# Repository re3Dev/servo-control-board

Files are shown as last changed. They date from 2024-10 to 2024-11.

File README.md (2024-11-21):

# servo-control-board
Breakout PCB for connecting external stepper/servo motor drivers.

- Takes digital pins from the Archimajor board (3.3V) and shifts voltage (0-50V) according to input using power drivers. 
- Maximum of 11 motors: 7 external, 4 TMC5160
- Display reads out supplied voltage for redundency.
- Pinout is simple and single-ended. Assuming motor driver takes step/pulse, direction, and enable. Currently no support for HLFB.
- Extra +5V and +3.3V output pins
- The main purpose of the project is to drive external servo motors, but other digital I/O devices can be used.

Soldered-V0 3

- Digital pins are taken from Serial 5V+, SC1, SC2, and step/dir header of the Archimajor board:
  




- NOTE:
  - The step/dir header on the archimajor are used for the last four stepper drivers.
  - These pins can be reassigned for external motors on the breakout board.
  - You cannot simultaneously drive an external motor and use the embedded drivers.

Archimajor_motors

- Design is made to primarily support Teknic Clearpath SD series motors.

clearpath_inputs

- Using single-ended connections (will need to invert logic):
  - A+ = Digital
  - B+ = Digital
  - EN+ = Digital
  - A- = GND
  - B- = GND
  - EN- = GND

- Pinout:
  - Motor1:
    - A+ = PA1
    - B+ = PC2
    - EN+ = PA28
  - Motor2:
    - A+ = PB13
    - B+ = PA0
    - EN+ = PB2
  - Motor3:
    - A+ = PB12
    - B+ = PA5
    - EN+ = PB25
  - Motor4:
    - A+ = PB27
    - B+ = PA3
    - EN+ = PB6
  - Motor5:
    - A+ = PB8
    - B+ = PB22
    - EN+ = PB3
  - Motor6:
    - A+ = PD3
    - B+ = PB24
    - EN+ = PB26
  - Motor7:
    - A+ = PA8
    - B+ = PA9
    - EN+ = PC8

top_unsoldered-V0 3
bottom_unsoldered-V0 3

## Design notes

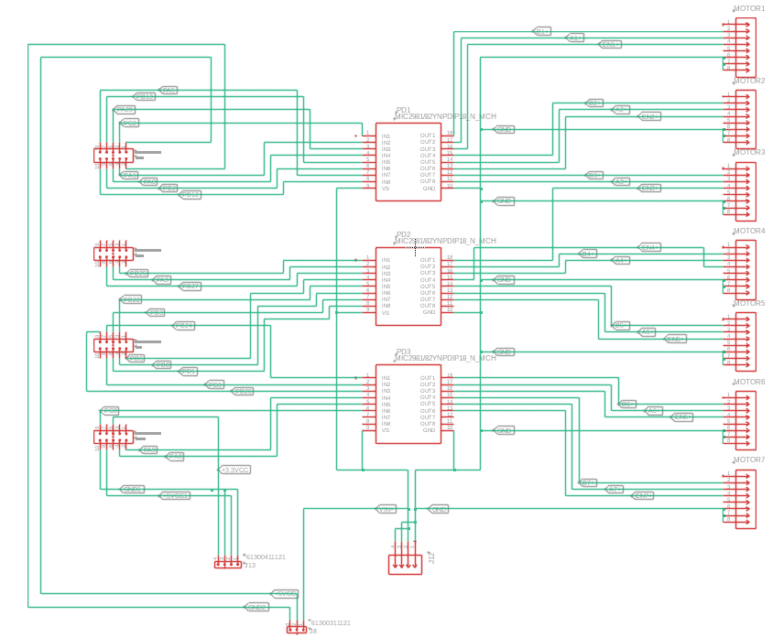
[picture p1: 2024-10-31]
Schematic_V0.3.png

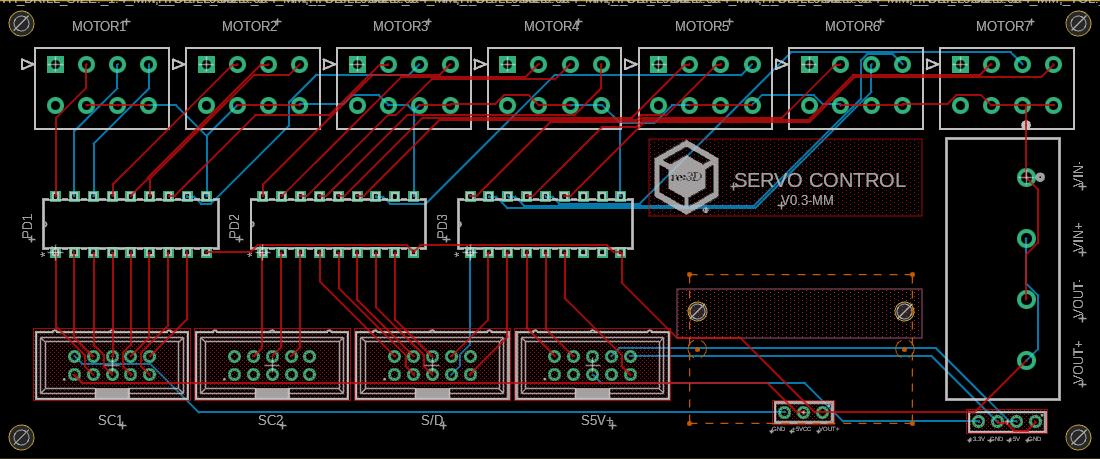
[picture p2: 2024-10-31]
PCB_V0.3.png

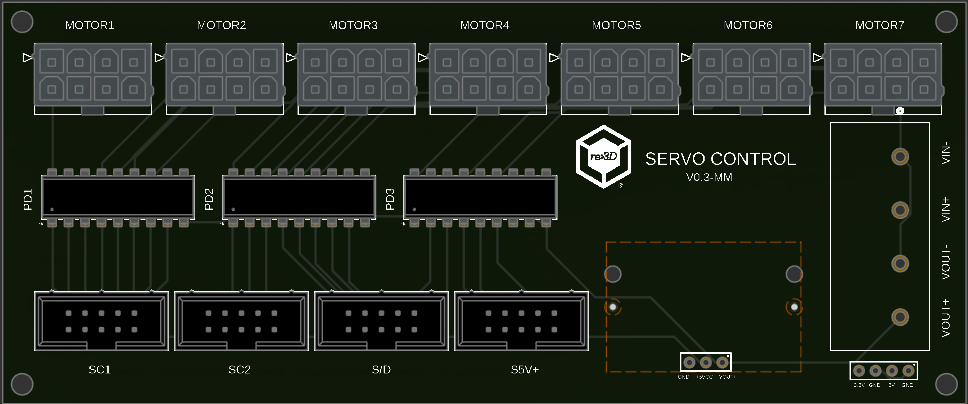
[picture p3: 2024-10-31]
3D_PCB_V0.3.png

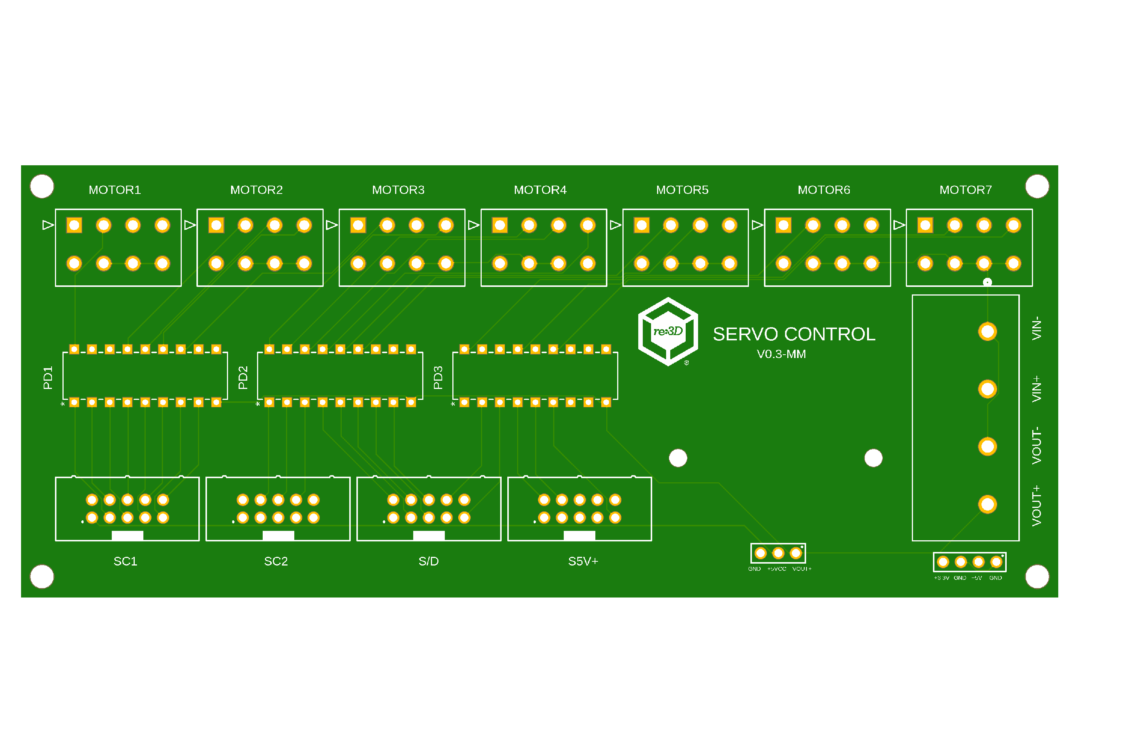
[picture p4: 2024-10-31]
PCB_Preview_V0.3.png

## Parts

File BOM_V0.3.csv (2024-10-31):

QUANTITY | PART NUMBER | MANUFACTURER | DESCRIPTION | PRICE PER UNIT(USD) | LINK
1 | OSTYK42104030 | On Shore Technology Inc. | 4 Circuit 0.325" (8.26mm) Barrier Block Connector Screws with Captive Plate | $1.47 | https://www.digikey.com/en/products/detail/on-shore-technology-inc/OSTYK42104030/1588754
4 | 61201021621 | Würth Elektronik | CONN HEADER VERT 10POS 2.54MM | $0.47 | https://www.digikey.com/en/products/detail/w%C3%BCrth-elektronik/61201021621/2060590?_gl=1*1gsermn*_up*MQ..
3 | MIC2981/82YN | Microchip Technology | Power Switch/Driver 1:1 Bipolar 500mA 18-DIP | $3.02 | https://www.digikey.com/en/products/detail/microchip-technology/MIC2981-82YN/771627
7 | 1724470208 | Molex | Connector Header Through Hole 8 position 0.165" (4.20mm) | $1.52 | https://www.digikey.com/en/products/detail/molex/1724470208/5405403
1 | 705 | Adafruit Industries LLC | VOLTMETER 0-99.9VDC LED CHAS MT | $7.95 | https://www.digikey.com/en/products/detail/adafruit-industries-llc/705/5353609
1 | 61300411121 | Würth Elektronik | CONN HEADER VERT 4POS 2.54MM | $0.19 | https://www.digikey.com/en/products/detail/w%C3%BCrth-elektronik/61300411121/4846827?gad_source=1

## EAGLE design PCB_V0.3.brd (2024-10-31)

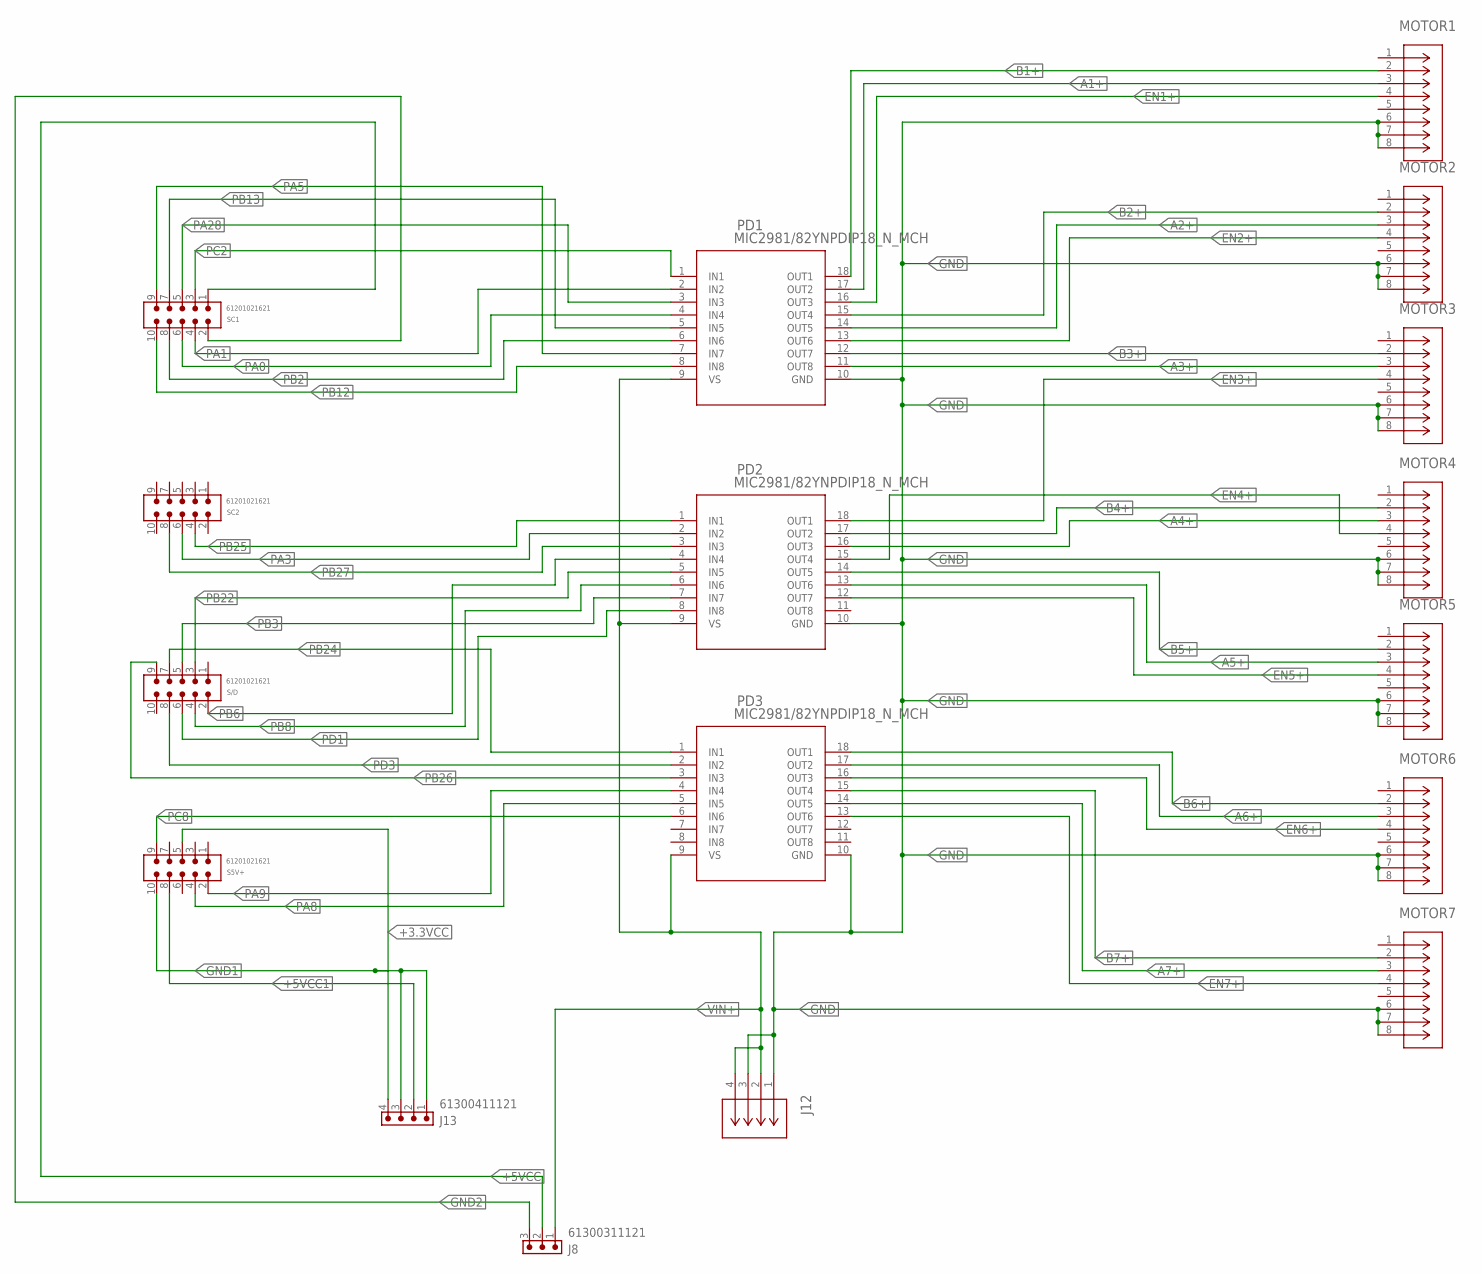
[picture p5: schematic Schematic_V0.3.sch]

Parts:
J8: 61300311121
J12: YK3310403000GCONN_YK331040XX00G_AMP; CONN_YK331040XX00G_AMP
J13: 61300411121
MOTOR1, MOTOR2, MOTOR3, MOTOR4, MOTOR5, MOTOR6, MOTOR7: 1724470208CON_1724470208; CON_1724470208
PD1, PD2, PD3: MIC2981/82YNPDIP18_N_MCH; PDIP18_N_MCH
S5V+: 61201021621
S/D: 61201021621
SC1, SC2: 61201021621

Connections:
+3.3VCC: J13.4, S5V+.5
+5VCC: J8.2, SC1.1
+5VCC1: J13.2, S5V+.8
A1+: MOTOR1.3, PD1.17 (OUT2)
A2+: MOTOR2.3, PD1.14 (OUT5)
A3+: MOTOR3.3, PD1.11 (OUT8)
A4+: MOTOR4.3, PD2.16 (OUT3)
A5+: MOTOR5.3, PD2.13 (OUT6)
A6+: MOTOR6.3, PD3.17 (OUT2)
A7+: MOTOR7.3, PD3.14 (OUT5)
B1+: MOTOR1.2, PD1.18 (OUT1)
B2+: MOTOR2.2, PD1.15 (OUT4)
B3+: MOTOR3.2, PD1.12 (OUT7)
B4+: MOTOR4.2, PD2.17 (OUT2)
B5+: MOTOR5.2, PD2.14 (OUT5)
B6+: MOTOR6.2, PD3.18 (OUT1)
B7+: MOTOR7.2, PD3.15 (OUT4)
EN1+: MOTOR1.4, PD1.16 (OUT3)
EN2+: MOTOR2.4, PD1.13 (OUT6)
EN3+: MOTOR3.4, PD2.18 (OUT1)
EN4+: MOTOR4.4, PD2.15 (OUT4)
EN5+: MOTOR5.4, PD2.12 (OUT7)
EN6+: MOTOR6.4, PD3.16 (OUT3)
EN7+: MOTOR7.4, PD3.13 (OUT6)
GND: J12.1, J12.3, MOTOR1.6, MOTOR1.7, MOTOR1.8, MOTOR2.6, MOTOR2.7, MOTOR2.8, MOTOR3.6, MOTOR3.7, MOTOR3.8, MOTOR4.6, MOTOR4.7, MOTOR4.8, MOTOR5.6, MOTOR5.7, MOTOR5.8, MOTOR6.6, MOTOR6.7, MOTOR6.8, MOTOR7.6, MOTOR7.7, MOTOR7.8, PD1.10 (GND), PD2.10 (GND), PD3.10 (GND)
GND1: J13.1, J13.3, S5V+.10
GND2: J8.3, SC1.2
PA0: PD1.4 (IN4), SC1.6
PA1: PD1.2 (IN2), SC1.4
PA3: PD2.2 (IN2), SC2.6
PA5: PD1.7 (IN7), SC1.9
PA8: PD3.5 (IN5), S5V+.4
PA9: PD3.4 (IN4), S5V+.2
PA28: PD1.3 (IN3), SC1.5
PB2: PD1.6 (IN6), SC1.8
PB3: PD2.7 (IN7), S/D.5
PB6: PD2.4 (IN4), S/D.2
PB8: PD2.6 (IN6), S/D.4
PB12: PD1.8 (IN8), SC1.10
PB13: PD1.5 (IN5), SC1.7
PB22: PD2.5 (IN5), S/D.3
PB24: PD3.1 (IN1), S/D.7
PB25: PD2.1 (IN1), SC2.4
PB26: PD3.3 (IN3), S/D.9
PB27: PD2.3 (IN3), SC2.8
PC2: PD1.1 (IN1), SC1.3
PC8: PD3.6 (IN6), S5V+.9
PD1: PD2.8 (IN8), S/D.6
PD3: PD3.2 (IN2), S/D.8
VIN+: J8.1, J12.2, J12.4, PD1.9 (VS), PD2.9 (VS), PD3.9 (VS)

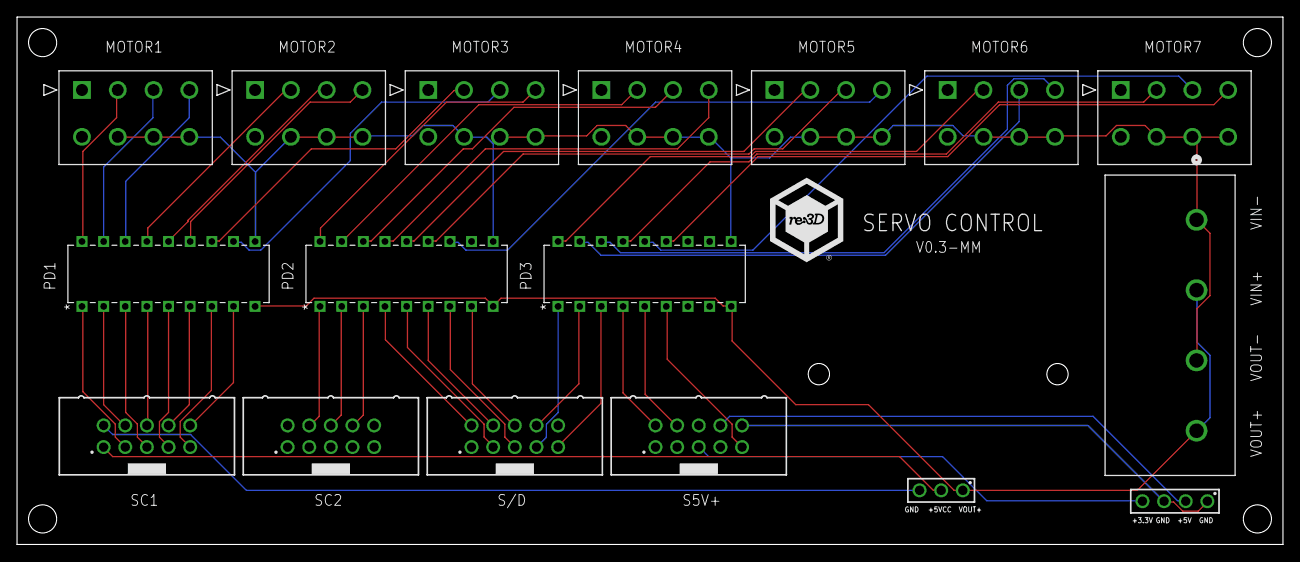
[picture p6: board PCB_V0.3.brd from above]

Board: 2 copper layers, 148.6 x 61.9 mm, 17 parts (0 on the bottom side), 50 nets.

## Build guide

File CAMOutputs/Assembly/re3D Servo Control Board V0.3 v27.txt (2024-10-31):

Partlist exported from Team Hub: re3D Gigabosses   Project: Mitchell  Board: re3D Servo Control Board V0.3 v27 at 10/31/2024 11:36 AM

Qty Value                               Device                              Package                Parts                                                  Description                    CONTACT-RESISTANCE COPYRIGHT                                                DATASHEET-URL                                           GENDER     IR LENGTH  MANUFACTURER_PART_NUMBER MFR_NAME                      MOUNT PACKAGING PART-NUMBER   PINS PITCH  ROWS   TYPE     VALUE         WORKING-VOLTAGE
4    61201021621                        6120XX21621_61201021621             61201021621            S/D, S5V+, SC1, SC2                                    WR-BHD 2.54 mm Male Box Header 20mOhm                                                                      https://www.we-online.com/redexpert/spec/61201021621?ae Male       3A 20.36mm                                                        THT   Tray       61201021621   10  2.54mm        Straight  61201021621  250V(AC)       
1    61300311121                        6130XX11121_61300311121             61300311121            J8                                                     WR-PHD 2.54 mm THT Pin Header                                                                              https://www.we-online.com/redexpert/spec/61300311121?ae Pin Header 3A                                                                THT   Bag        61300311121   3   2.54mm Single Straight  61300311121                 
1    61300411121                        6130XX11121_61300411121             61300411121            J13                                                    WR-PHD 2.54 mm THT Pin Header                                                                              https://www.we-online.com/redexpert/spec/61300411121?ae Pin Header 3A                                                                THT   Bag        61300411121   4   2.54mm Single Straight  61300411121                 
7   1724470208CON_1724470208            1724470208CON_1724470208            CON_1724470208         MOTOR1, MOTOR2, MOTOR3, MOTOR4, MOTOR5, MOTOR6, MOTOR7                                                   Copyright (C) 2024 Ultra Librarian. All rights reserved.                                                                               1724470208               Molex Connector Corporation                                                                                          
3   MIC2981/82YNPDIP18_N_MCH            MIC2981/82YNPDIP18_N_MCH            PDIP18_N_MCH           PD1, PD2, PD3                                                                                            Copyright (C) 2024 Ultra Librarian. All rights reserved.                                                                               MIC2981/82YN             Micrel / Microchip Technology                                                                                        
1   YK3310403000GCONN_YK331040XX00G_AMP YK3310403000GCONN_YK331040XX00G_AMP CONN_YK331040XX00G_AMP J12                                                                                                      Copyright (C) 2024 Ultra Librarian. All rights reserved.                                                                               YK3310403000G            Amphenol ICC

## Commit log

2024-10-17 Add in files.
    [3D_PCB_V0.1.3mf, BOM_V0.1.csv, PCB_V0.1.brd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]
2024-10-29 Update files to V0.2
    [3D_PCB_V0.1.3mf, BOM_V0.1.csv, BOM_V0.2.csv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]
2024-10-31 Import V0.3 files
    [BOM_V0.2.csv, BOM_V0.3.csv, PCB_V0.2.brd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]

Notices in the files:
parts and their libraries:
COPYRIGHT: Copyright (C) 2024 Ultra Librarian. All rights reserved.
